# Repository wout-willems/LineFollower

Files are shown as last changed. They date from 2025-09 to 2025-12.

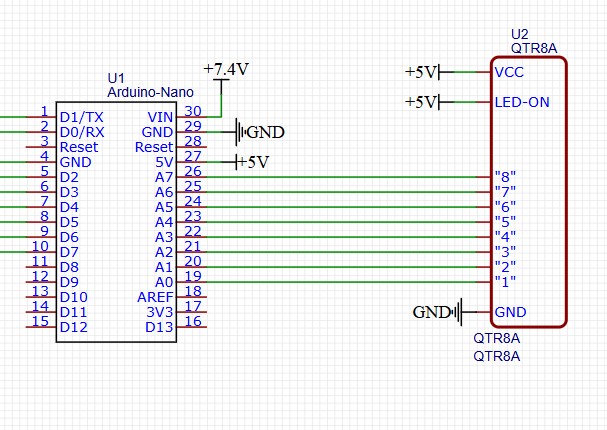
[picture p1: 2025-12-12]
code/proof of concepts/sensor/sensor_schema.jpg

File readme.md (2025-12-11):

# LineFollower



## specifications

microcontroller: arduino nano

motors: N20 micro metal gears

h-bridge: TB6612FNG

sensors: QTR-8A

batteries: LiPo 18650

wireless communication: HC-05

distance sensor - motors: 11cm

weight: /

speed: /

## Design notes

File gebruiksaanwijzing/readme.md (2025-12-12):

# Gebruiksaanwijzing

### opladen / vervangen batterijen
De batterijen kunnen opgeladen worden door de oplaadmodule(3 kabels aan de batterij) in een speciale oplader te bevestigen.

### draadloze communicatie
#### verbinding maken
er is geen draadloze verbinding mogelijk, je kan de robot wel altijd bekabeld verbinden met een laptop en zo de code aanpassen via de Arduino IDE app.

#### commando's
debug [on/off]  
run: de robot start met het parcours  
stop: de robot stopt onmiddelijk
set power [0..200] : hiermee bepaal je de gemiddelde snelheid waarmee de robot het parcours aflegt  
set kp [0-10]  : dit verhoogt/verlaagt de proportionele waarde waarme de ronot fouten zal corrigeren
set ki [0-10]  : dit verhoogt/verlaagt de integrale waarde waarme de ronot fouten zal corrigeren
set kd [0-10]  : dit verhoogt/verlaagt de differentiële waarde waarme de ronot fouten zal corrigeren
calibrate black  : hiermee kalibreer je de standaard zwarte kleur
calibrate white  : hiermee kalibreer je de standaard witte kleur

### kalibratie
via de commando's calibrate black/white kan je de waarden die als zwart of wit worden gerekend fine-tunen. Je hoeft enkel de robot op een volledig zwarte/witte ondergrond te houden en de commando's in te voeren.
Het is aangeraden om dit vrij frequent te doen, zo vermijd je impact van zon, schaduw, lampen...
### settings
Power = 100;
kp = 6.7;
ki = 0;
kd = 4;  

### start/stop button
De rode schakelaar kan gebruikt worden om het programma te starten/stoppen, deze bevindt zich in het midden van de printplaat. De status (start/stop) wordt ook visueel bevestigd door een blauw LED-lampje. Het volledig uitschakelen van de robot kan via de zwarte schakelaar achteraan de robot.

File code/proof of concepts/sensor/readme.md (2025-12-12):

# Sensoren proof of concept

De sensoren moeten boven een zwart/wit blad gehouden worden (3-10 mm hoogte) de sensoren die boven een zwart deel zitten zullen een lage waarde hebben en de sensoren die boven een zwart deel hangen zullen een hogere waarde hebben. (bereik: 0-1023)

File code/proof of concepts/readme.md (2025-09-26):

# Proof of Concepts

Een proof of concept is een combinatie van minimale hard- en software om eenvoudig aan te tonen dat iets werkt.  
Proof of concepts kunnen enerzijds als eerste poging dienen om een bepaald onderdeel van het project werkend te krijgen. Anderzijds kunnen ze tijdens het debuggen van het finale project dienen als test om eventuele hardware problemen te elimineren bij onduidelijke problemen.
<br />  
<br />
Een proof of concept bestaat uit
* een elektronisch schema (indien van toepassing)
* minimale code om de voorop gestelde zaken te demonstreren
* minimale uitleg / aandachtspunten
<br />
De elektronische schakelingen van de proof of concepts komen bij voorkeur overeen met deze van de uiteindelijke linefollower, zodat de code zonder aanpassingen op het finale project kan draaien.

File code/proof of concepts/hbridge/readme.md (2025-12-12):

# H-Bridge proof of concept

Je schakelt de schakelaar aan, vervolgens zal de robot geleidelijk vooruit versnellen, dan stopt hij en zal hij achteruit versnellen. Hierna zullen beide wielen in tegengestelde richting versnellen en hierna wisselen ze nog eens om van richting.

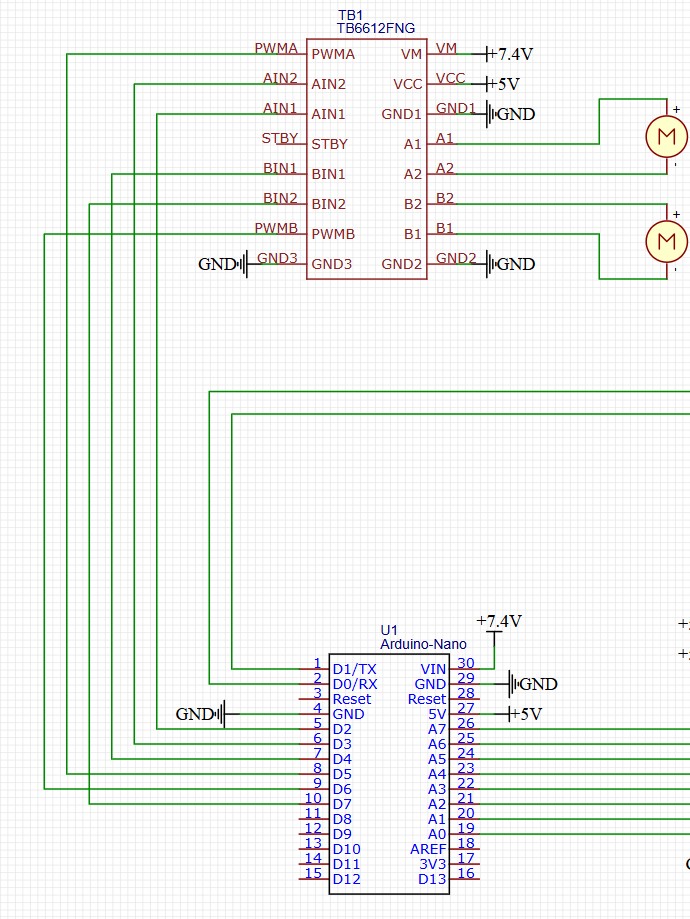
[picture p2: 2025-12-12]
code/proof of concepts/hbridge/h-brug_schema.jpg

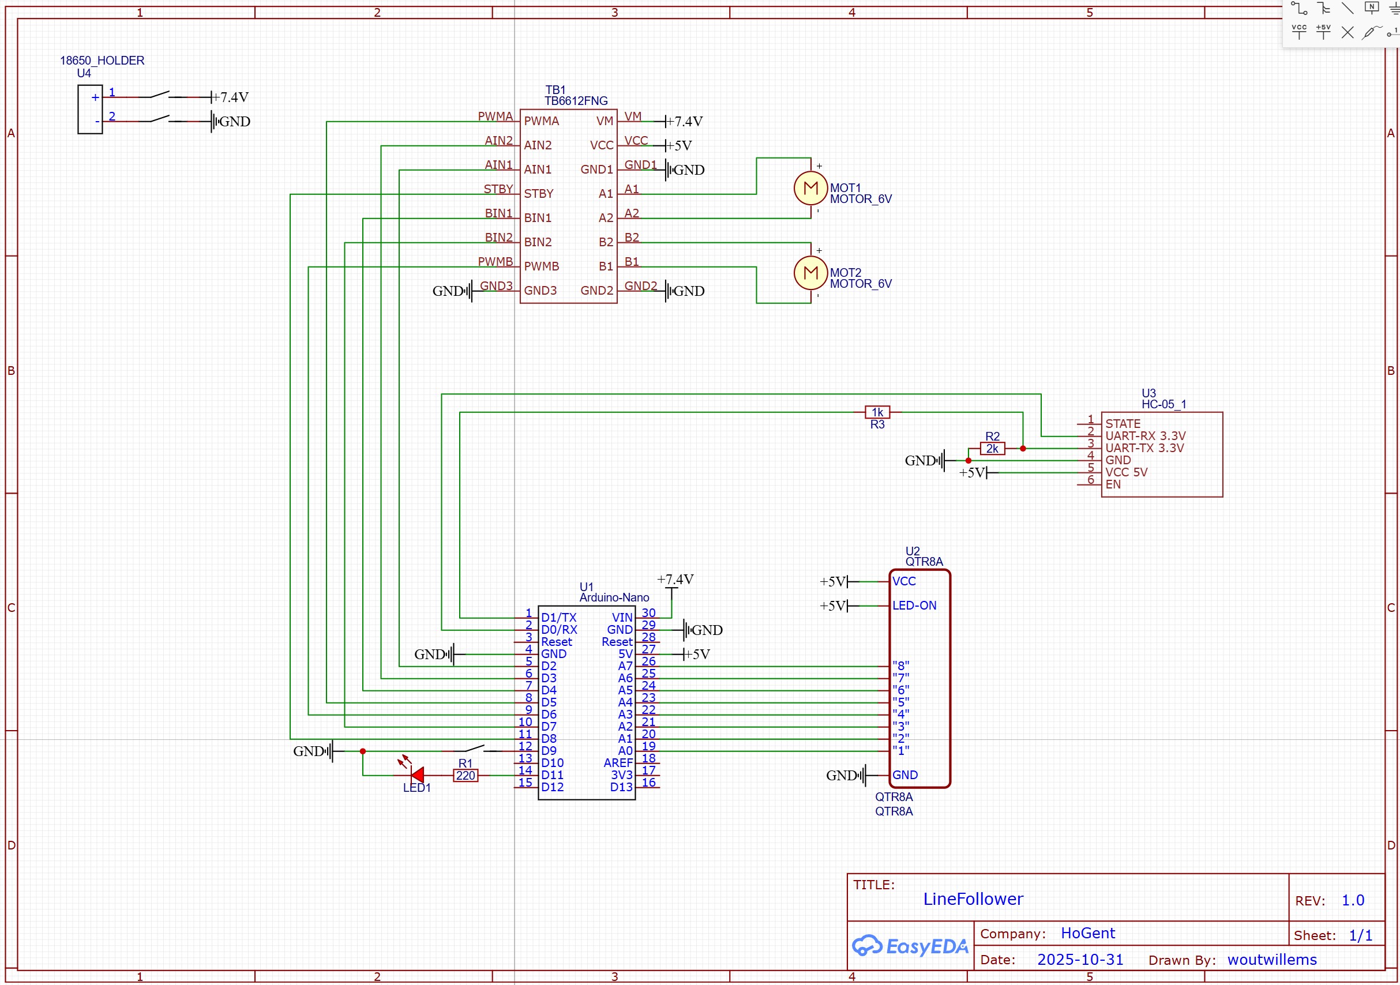
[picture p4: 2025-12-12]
technische tekeningen/elektronisch/elektronisch.jpg

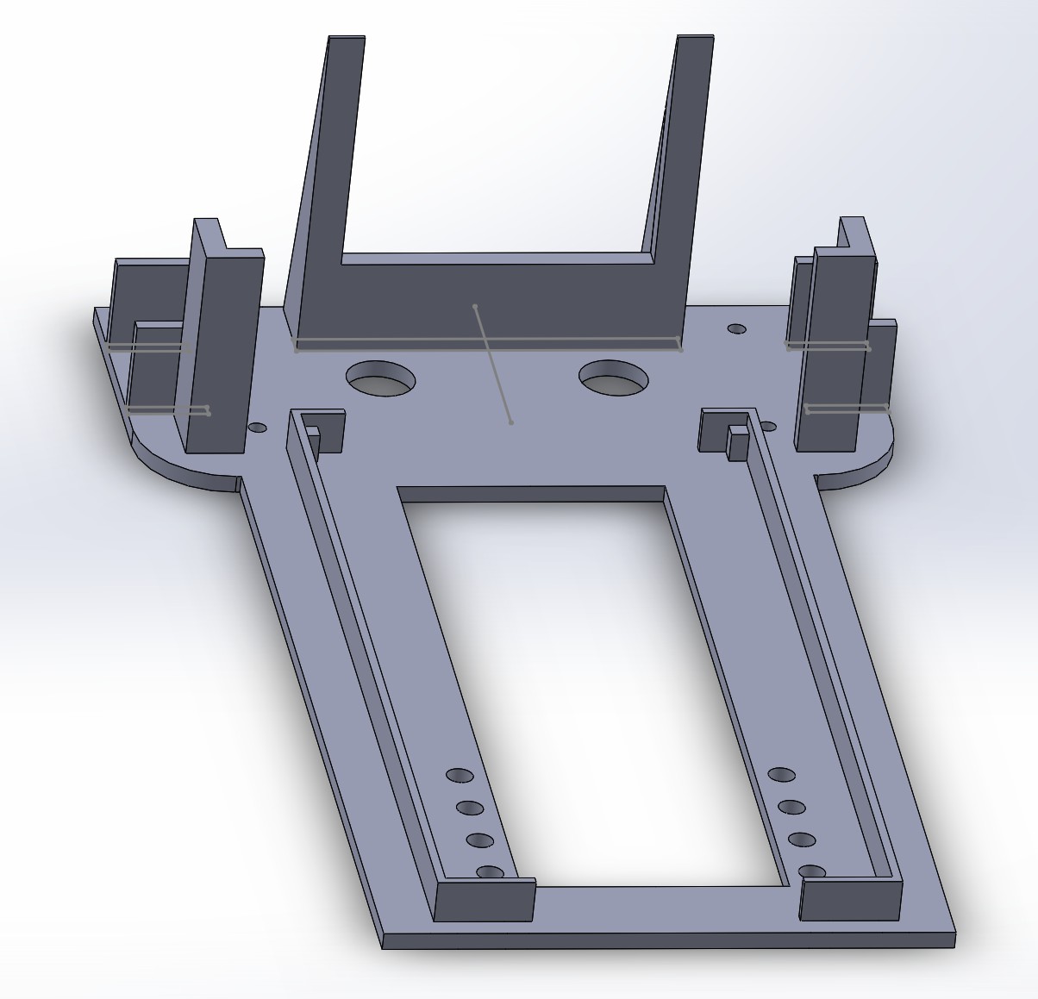
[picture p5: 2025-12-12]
technische tekeningen/mechanisch/frame_foto.jpg

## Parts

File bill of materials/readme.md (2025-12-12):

## bill of materials
<br />

|volgnummer|naam|omschrijving|nieuw/recup|kostprijs/stuk|aantal|subtotaal|
|---|----|---|---|---|---|---|
| 1|motoren|N20 micro metal gear motors (30:1)|nieuw|€2.64|2|€5.28|
| 2|batterijen|Lithium 18650|nieuw|€8.42|1|€8.42|
| 3|H-brug|TB6612FNG|nieuw|€1.07|1|€1.07|
| 4|Sensoren|HY-S301|nieuw|€2.99|1|€2.99|
| 5|bluetooth|HC-05|nieuw|€7.99|1|€7.99|
| 6|microcontroller|arduino nano|recup|€6.80|1|€6.80|
| 7|wielen|⌀34|nieuw|€0.35|2|€0.70|
| 8|Frame|3D-print|nieuw|€1.20|1|€1.20|
| 9|weerstanden|1kΩ|recup|€0|3|€0|
| 10|schakelaar|dubbelpolig|recup|€0|1|€0|
| TOTAAL||||||€34.45|

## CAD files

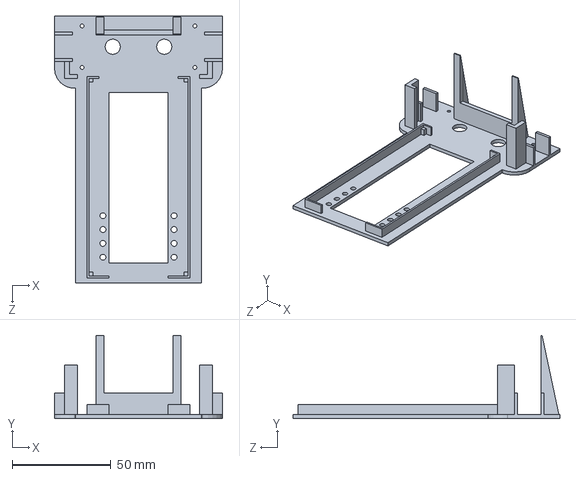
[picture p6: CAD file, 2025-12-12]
technische tekeningen/mechanisch/Frame.SLDPRT
85.0 x 42.0 x 135.0 mm

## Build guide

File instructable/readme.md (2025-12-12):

# Instructable

### stap 1
bestel alle componenten uit de bill of materials  
### stap 2
download het frame via SolidWorks en print het
### stap 3
soldeer de bestelde componenten op de printplaat (kijk goed uit waar welke weerstanden moeten!)
### stap 4
bevestig de sensor onderaan het frame samen met moeren die hem van de grond houden  
### stap 5
monteer de motortjes in hun houder en bevestig met schroeven
### stap 6
connecteer de batterij met de printplaat en verbind de arduino met uw laptop
### stap 7
open arduino IDE op uw laptop en importeer de code
### stap 8
upload de code naar de microcontroller en deconnecteer uw laptop van de arduino
### stap 9
Voila, u kunt de robot bedienen via de schakelaars

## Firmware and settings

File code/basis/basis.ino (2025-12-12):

#include <EEPROM.h>

// ---------- PIN DEFINITIES ----------
int MotorLeftForward = 3;
int MotorLeftBackward = 2;
int MotorLeftPWM = 5;

int MotorRightForward = 4;
int MotorRightBackward = 7;
int MotorRightPWM = 6;

int STBY = 8;

const int buttonPin = 9;
const int ledPin = 10;

// ---------- SENSOR PINNEN ----------
const int sensor[] = { A0, A1, A2, A3, A4, A5, A6, A7 };
int normalised[8];
const float sensorSpacing = 9.525; // afstand tussen sensoren in mm

// ---------- PARAMETERS ----------
int basePower = 25;      // basissnelheid motoren
float kp = 1.2;           // proportionele factor
float ki = 0;          // integrerende factor
float kd = 0;           // differentiële factor

int black[8];             // zwarte referentiewaarden
int white[8];             // witte referentiewaarden

bool run = true;         // of de robot mag rijden

// PID variabelen
float iTerm = 0;
float lastError = 0;

// ---------- SETUP ----------
void setup() {
  Serial.begin(115200);

  // Motor pins
  pinMode(MotorLeftForward, OUTPUT);
  pinMode(MotorLeftBackward, OUTPUT);
  pinMode(MotorLeftPWM, OUTPUT);
  pinMode(MotorRightForward, OUTPUT);
  pinMode(MotorRightBackward, OUTPUT);
  pinMode(MotorRightPWM, OUTPUT);
  pinMode(STBY, OUTPUT);
  digitalWrite(STBY, HIGH);

  pinMode(buttonPin, INPUT_PULLUP);
  pinMode(ledPin, OUTPUT);

  // Sensoren
  for(int i=0; i<8; i++) pinMode(sensor[i], INPUT);

  // EEPROM uitlezen
  EEPROM.get(0, black);
  EEPROM.get(sizeof(black), white);

  Serial.println("Linefollowing PID start. Gebruik 'calibrate black', 'calibrate white', 'run' of 'stop'.");
}

// ---------- LOOP ----------
void loop() {
  // ----- Seriële commando's uitlezen -----
  if (Serial.available()) {
    String command = Serial.readStringUntil('\n');
    command.trim();

    if(command == "calibrate black") {
      Serial.println("Calibrating black...");
      for(int i=0; i<8; i++){
        black[i] = analogRead(sensor[i]);
      }
      EEPROM.put(0, black);
      Serial.println("Black calibration done.");
    }
    else if(command == "calibrate white") {
      Serial.println("Calibrating white...");
      for(int i=0; i<8; i++){
        white[i] = analogRead(sensor[i]);
      }
      EEPROM.put(sizeof(black), white);
      Serial.println("White calibration done.");
    }
    else if(command == "run") {
      run = true;
      digitalWrite(ledPin, HIGH);
      Serial.println("Robot is running!");
    }
    else if(command == "stop") {
      run = false;
      digitalWrite(ledPin, LOW);
      Serial.println("Robot stopped!");
      // Zet motoren direct uit
      analogWrite(MotorLeftPWM, 0);
      analogWrite(MotorRightPWM, 0);
      digitalWrite(MotorLeftForward, LOW);
      digitalWrite(MotorLeftBackward, LOW);
      digitalWrite(MotorRightForward, LOW);
      digitalWrite(MotorRightBackward, LOW);
      iTerm = 0; // reset integratie
      lastError = 0;
    }
  }

if(digitalRead(buttonPin) == LOW) {
      run = true;
      digitalWrite(ledPin, HIGH);
      Serial.println("Robot is running!");
    }
    else if(digitalRead(buttonPin) == HIGH) {
      run = false;
      digitalWrite(ledPin, LOW);
      Serial.println("Robot stopped!");
      // Zet motoren direct uit
      analogWrite(MotorLeftPWM, 0);
      analogWrite(MotorRightPWM, 0);
      digitalWrite(MotorLeftForward, LOW);
      digitalWrite(MotorLeftBackward, LOW);
      digitalWrite(MotorRightForward, LOW);
      digitalWrite(MotorRightBackward, LOW);
      iTerm = 0; // reset integratie
      lastError = 0;
    }


  if(!run) return; // stop als run = false

  // ----- Sensoren normaliseren -----
  for(int i=0; i<8; i++){
    normalised[i] = map(analogRead(sensor[i]), black[i], white[i], 0, 1000);
  }

  // ----- Positie berekenen in mm -----
  float weightedPosition = 0;
  int sum = 0;
  for(int i=0; i<8; i++){
    int value = 1000 - normalised[i]; // zwart = hoog
    weightedPosition += i * value;
    sum += value;
  }

  float position_mm = 0;
  if(sum > 0) {
    float centerIndex = weightedPosition / sum;
    position_mm = (centerIndex - 3.2) * sensorSpacing; // gecentreerd rond 0 mm
  }

  float error = -position_mm;

  // ----- PID berekening -----
  iTerm += ki * error;
  iTerm = constrain(iTerm, -200, 200); // voorkom integrale windup
  float dTerm = kd * (error - lastError);
  lastError = error;

  float correction = kp * error + iTerm + dTerm;

  int powerLeft = basePower + correction;
  int powerRight = basePower - correction;

  // Limiteer motorvermogen
  powerLeft = constrain(powerLeft, 0, 200);
  powerRight = constrain(powerRight, 0, 200);

  // ----- Motoren aansturen -----
  if(powerLeft >= 0){
    digitalWrite(MotorLeftForward, HIGH);
    digitalWrite(MotorLeftBackward, LOW);
  } else {
    digitalWrite(MotorLeftForward, LOW);
    digitalWrite(MotorLeftBackward, HIGH);
    powerLeft = -powerLeft;
  }
  analogWrite(MotorLeftPWM, powerLeft);

  if(powerRight >= 0){
    digitalWrite(MotorRightForward, HIGH);
    digitalWrite(MotorRightBackward, LOW);
  } else {
    digitalWrite(MotorRightForward, LOW);
    digitalWrite(MotorRightBackward, HIGH);
    powerRight = -powerRight;
  }
  analogWrite(MotorRightPWM, powerRight);

  delay(10);
}

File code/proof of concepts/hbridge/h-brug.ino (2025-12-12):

// Pin definities
int AIN1 = 3;
int AIN2 = 2;
int PWMA = 5;

int BIN1 = 4;
int BIN2 = 7;
int PWMB = 6;

int STBY = 8;

// Maximale PWM zodat motoren effectief ~6V krijgen op 7.4V voeding
// Je kan hiermee "power reduceren"
int MAX_PWM = 100;  // 0–255

void setup() {
  pinMode(AIN1, OUTPUT);
  pinMode(AIN2, OUTPUT);
  pinMode(PWMA, OUTPUT);

  pinMode(BIN1, OUTPUT);
  pinMode(BIN2, OUTPUT);
  pinMode(PWMB, OUTPUT);

  pinMode(STBY, OUTPUT);

  digitalWrite(STBY, HIGH);  // driver activeren
}

void loop() {


  for (int i = 0; i <= 150; i++) {

    digitalWrite(AIN1, HIGH);
    digitalWrite(AIN2, LOW);
    analogWrite(PWMA, i);

    digitalWrite(BIN1, HIGH);
    digitalWrite(BIN2, LOW);
    analogWrite(PWMB, i);
    delay(10);
  }

  delay(1000);

  analogWrite(PWMA, 0);
  analogWrite(PWMB, 0);

  delay(3000);







  for (int i = 0; i <= 150; i++) {

    digitalWrite(AIN1, LOW);
    digitalWrite(AIN2, HIGH);
    analogWrite(PWMA, i);

    digitalWrite(BIN1, LOW);
    digitalWrite(BIN2, HIGH);
    analogWrite(PWMB, i);
    delay(10);
  }

    delay(1000);

  analogWrite(PWMA, 0);
  analogWrite(PWMB, 0);

  delay(3000);







  for (int i = 0; i <= 70; i++) {

    digitalWrite(AIN1, HIGH);
    digitalWrite(AIN2, LOW);
    analogWrite(PWMA, i);

    digitalWrite(BIN1, LOW);
    digitalWrite(BIN2, HIGH);
    analogWrite(PWMB, i);
    delay(10);
  }

    delay(1000);

  analogWrite(PWMA, 0);
  analogWrite(PWMB, 0);

  delay(3000);








  for (int i = 0; i <= 70; i++) {

    digitalWrite(AIN1, LOW);
    digitalWrite(AIN2, HIGH);
    analogWrite(PWMA, i);

    digitalWrite(BIN1, HIGH);
    digitalWrite(BIN2, LOW);
    analogWrite(PWMB, i);
    delay(10);
  }

    delay(1000);

  analogWrite(PWMA, 0);
  analogWrite(PWMB, 0);

  delay(3000);
}
